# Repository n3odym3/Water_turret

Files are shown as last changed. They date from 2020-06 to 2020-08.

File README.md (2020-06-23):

# Water turret

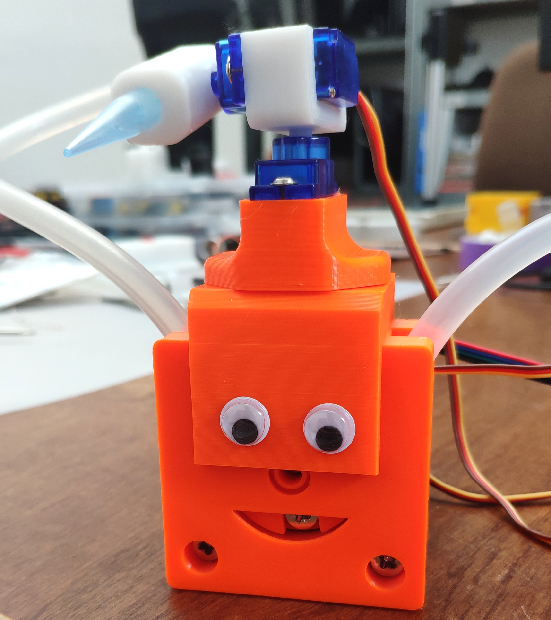
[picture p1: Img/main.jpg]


This water turret uses a WemoD1, two 9g servo motors, a Nema17 stepper motor (+DRV8825 driver) and 3D printed parts to create a water turret that can be remotely controlled via MQTT and automatically aims and shoot water at different locations.

## Supplies
- 6x bearings 13x4x5mm
- 6x M4 washers
- 7x M4 nuts
- 3x M4x15
- 4x M4x25
- 2x M3x13
- 7mm silicone tube
- P1000 micropipette Tip
- 4x 10x3mm neodymium magnets

## Wiring
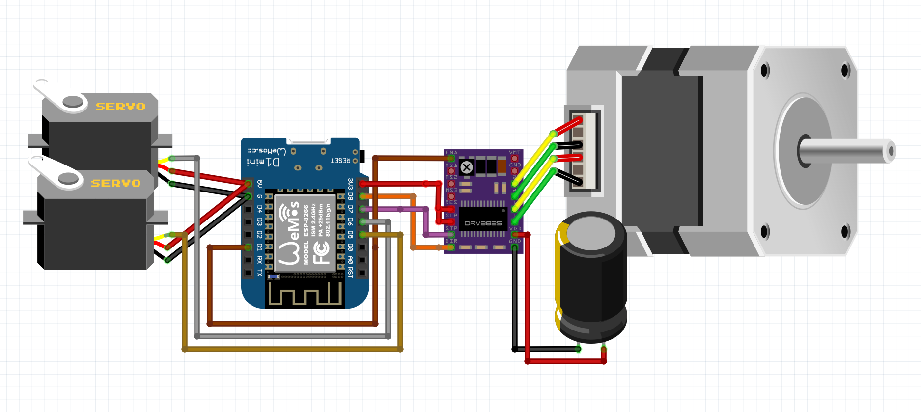
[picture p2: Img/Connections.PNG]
 \
- Servo 1 : D5 (GPIO 14)
- Servo 2 : D6 (GPIO 12)
- DIR : D8 (GPIO 15)
- STEP : D7 (GPIO 14)
- EN : D1 (GPIO 05)
## Control
The robot can be controlled by sending simple JSON commands :
- X axis : {"X": 0 to 180}
- Y axis : {"Y": 0 to 180}
- Pump : {"P" : steps (200 steps/rotation)} \
Ex : {"X": 30, "Y":50} then {"P": 10000}

## NodeRed demo
The demo on NodeRed (installed on a Raspberry Pi zero) allows to test and remote control the robot.\
Sensors and advances automation sequences could be added to the flow to water several plants depending on soil moisture or add a camera with motion detection to make an anti-intrusion system or anything else.

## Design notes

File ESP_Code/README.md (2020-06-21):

# Dependencies
- ArduinoJson6

## Included
- ESP8266WiFi
- PubSubClient
- Servo

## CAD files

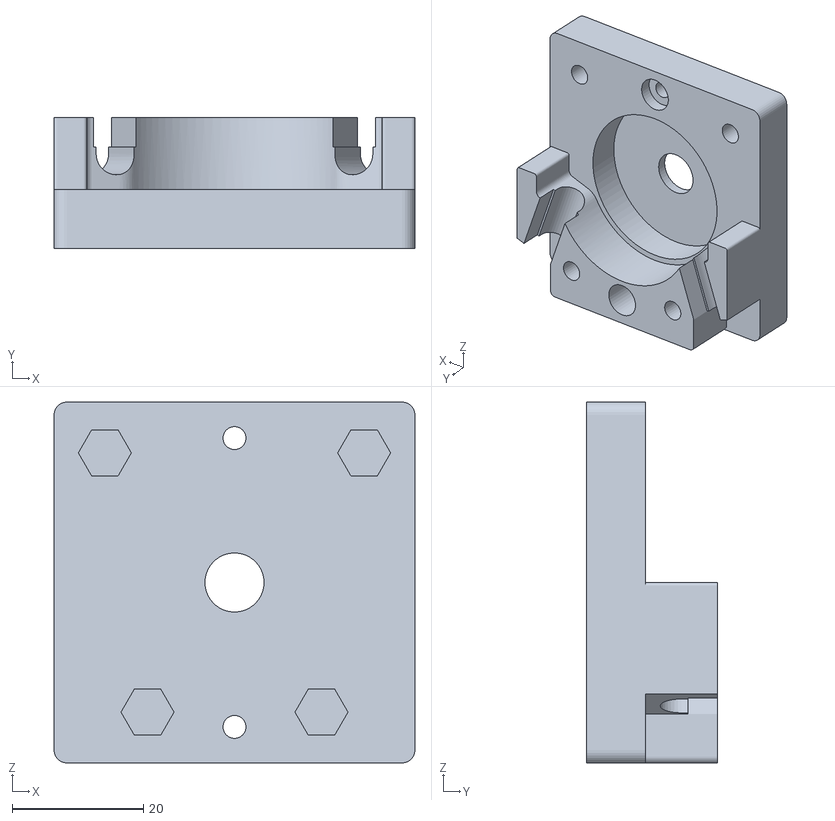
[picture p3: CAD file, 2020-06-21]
3D Files/Stator Main.stl
55.0 x 20.0 x 55.0

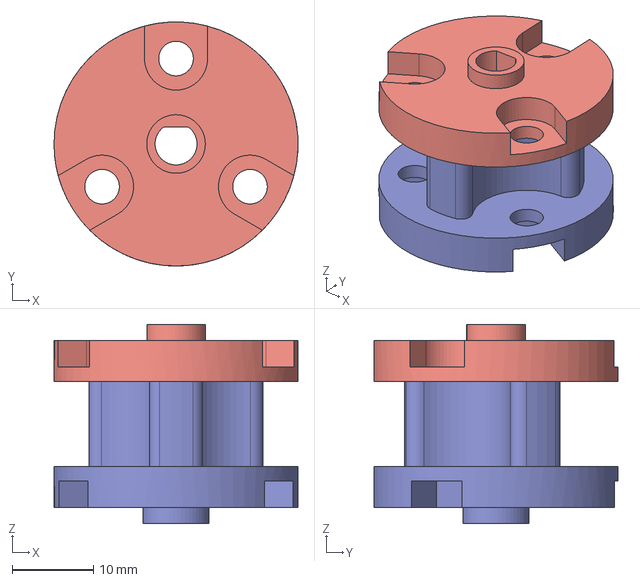
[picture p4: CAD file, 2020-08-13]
3D Files/Rotor.step
30.0 x 30.0 x 24.5 mm

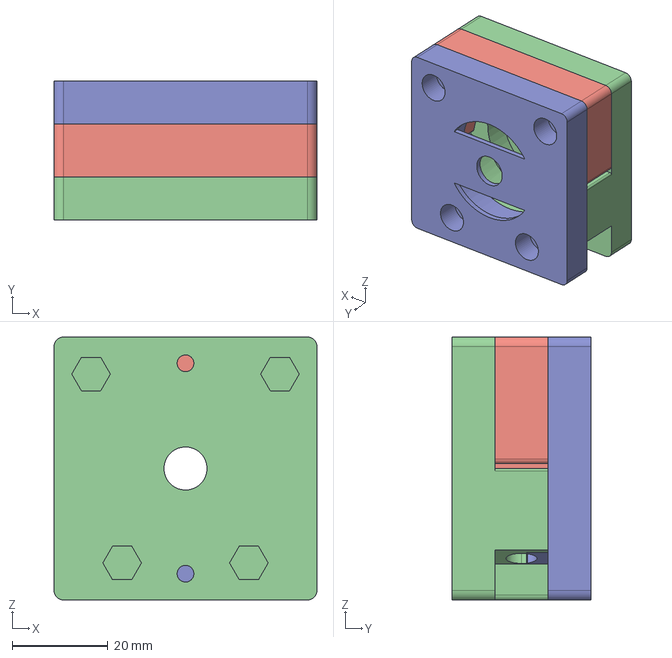
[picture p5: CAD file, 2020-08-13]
3D Files/Stator.step
55.0 x 29.0 x 55.0 mm

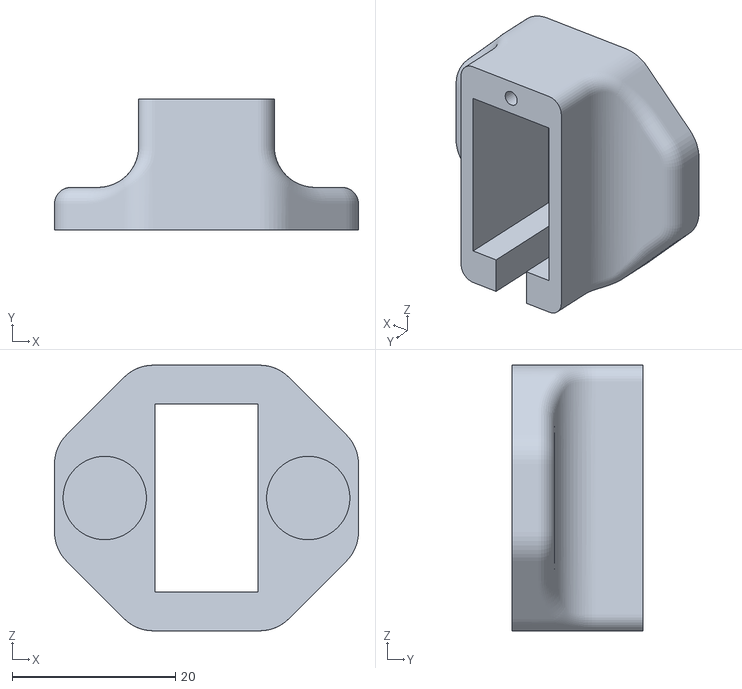
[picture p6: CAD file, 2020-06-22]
3D Files/X_Holder.stl
37.2 x 16.0 x 32.5

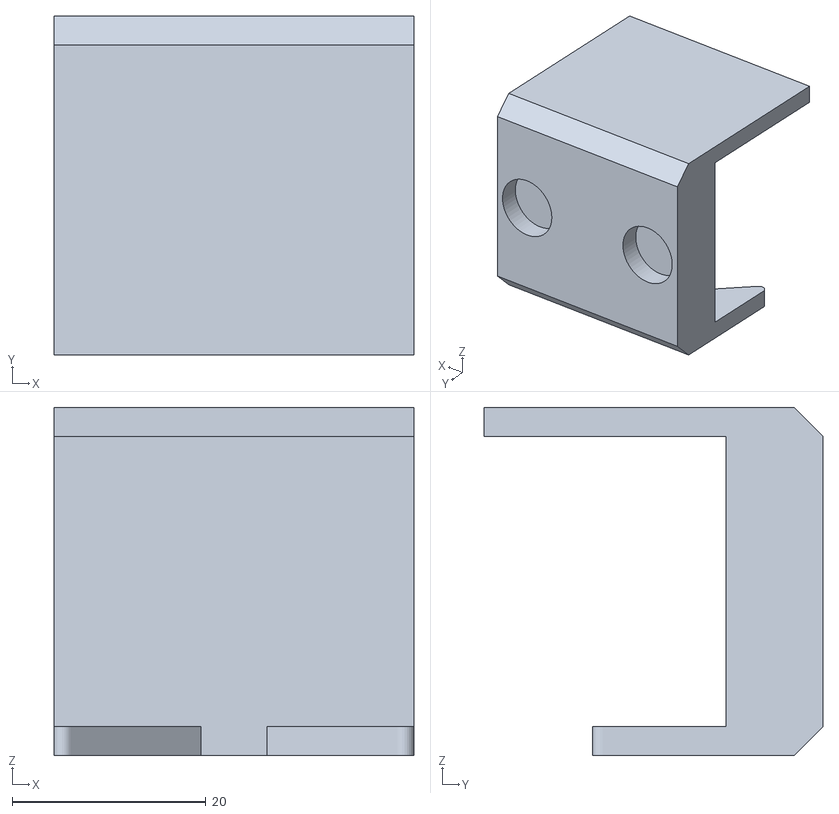
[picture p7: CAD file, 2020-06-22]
3D Files/Motor_Support.stl
37.2 x 35.0 x 36.0

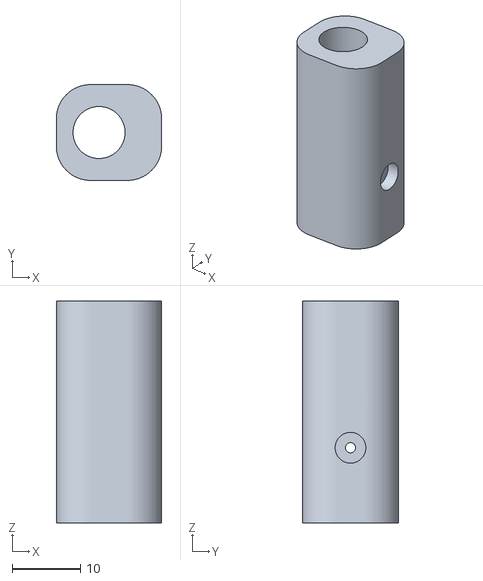
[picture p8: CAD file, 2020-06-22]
3D Files/Tip_Holder.stl
15.4 x 14.0 x 32.4

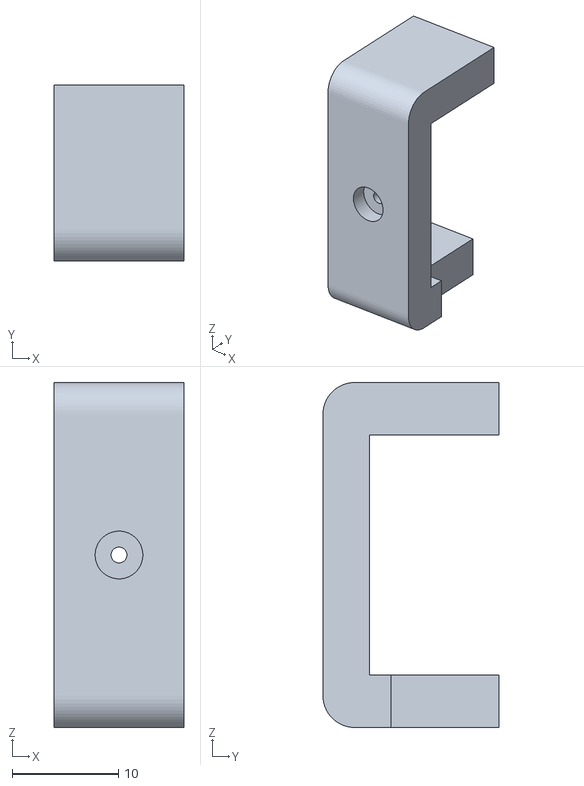
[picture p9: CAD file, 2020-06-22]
3D Files/Y_Holder.stl
12.2 x 16.6 x 32.5

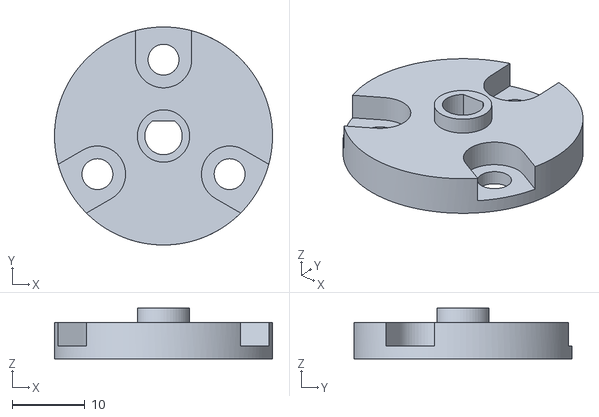
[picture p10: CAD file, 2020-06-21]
3D Files/RotorB.stl
30.0 x 30.0 x 7.00

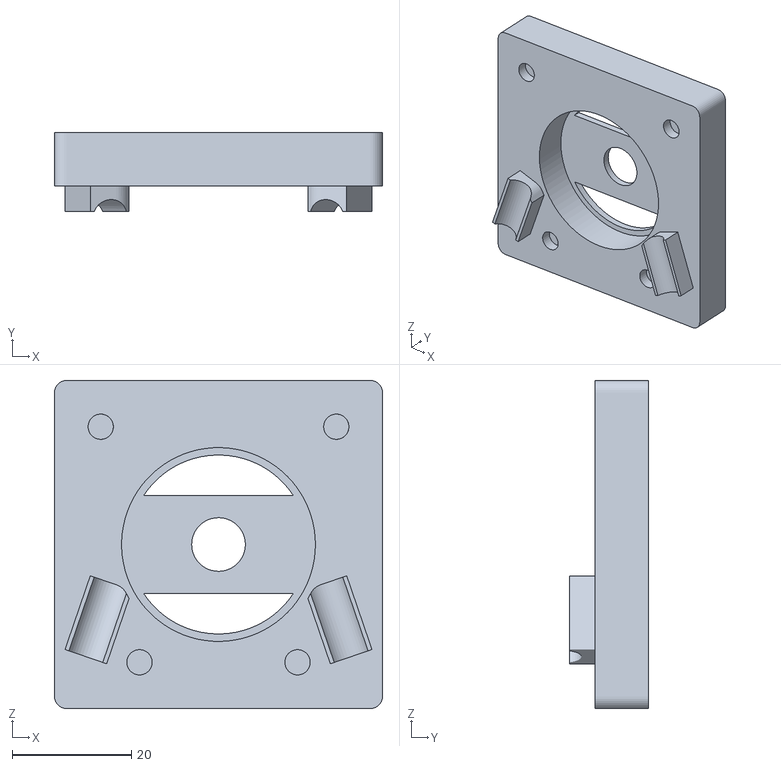
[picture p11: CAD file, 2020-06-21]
3D Files/Stator Lock.stl
55.0 x 13.2 x 55.0

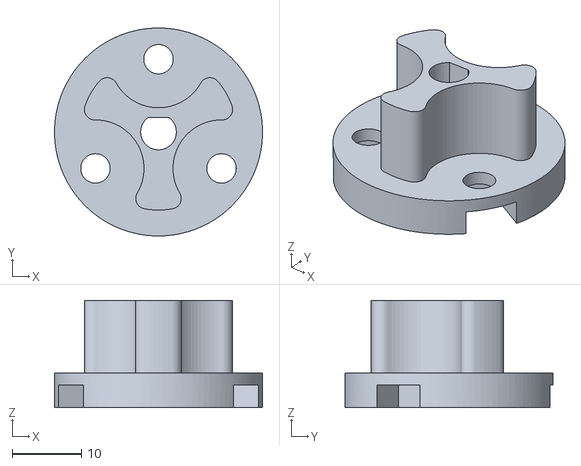
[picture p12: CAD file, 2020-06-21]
3D Files/RotorA.stl
30.0 x 30.0 x 15.5

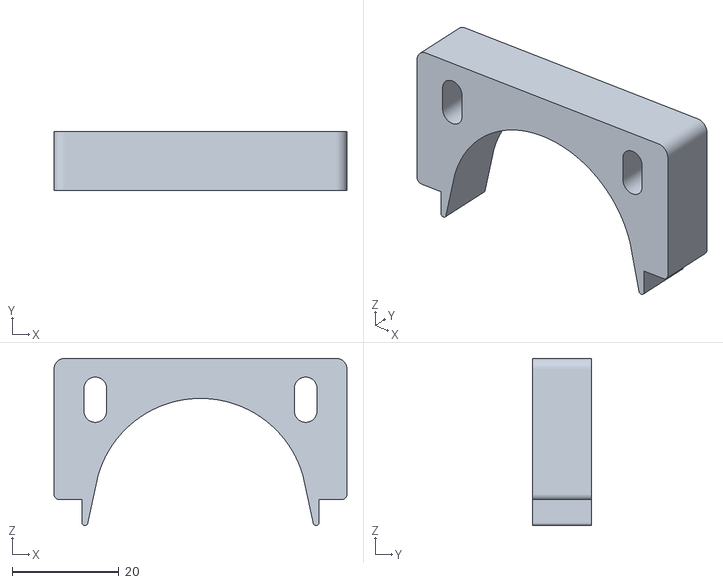
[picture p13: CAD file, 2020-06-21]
3D Files/Lock.stl
55.0 x 11.0 x 31.4

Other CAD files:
3D Files/Rotor.f3d
3D Files/Stator.f3d

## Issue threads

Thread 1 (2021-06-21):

Issue on drv8825 schematic

DaspRoot, 2021-06-21:
In Connections.PNG, there are two mistakes on the schematic:
-The capacitor should be on the step motor supply (VMT and GND)
-Then there is no VDD but rather FLT/

Sorry for the inconvenience

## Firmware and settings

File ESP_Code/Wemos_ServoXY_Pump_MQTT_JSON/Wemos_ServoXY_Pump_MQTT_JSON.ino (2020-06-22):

#include <ESP8266WiFi.h>
#include <PubSubClient.h>
#include <ArduinoJson.h> //ArduinoJSON6
DynamicJsonDocument Input(2048);
#include "config.h"

#include <Servo.h>
Servo ServoX;
Servo ServoY;

#define RPM 200
#define DIR 15// D8
#define STEP 13// D7
#define EN 5// D1

WiFiClient espClient;
PubSubClient client(espClient);

class StepperDriver {
  public:
    short dir_pin, step_pin, en_pin;
    int delay_step = 500;
    StepperDriver(): dir_pin(0), step_pin(0), en_pin(0) {}
    StepperDriver(short dir_pin, short step_pin, short en_pin) : dir_pin(dir_pin), step_pin(step_pin), en_pin(en_pin) {}

    void begin(int rpm) {
      pinMode(dir_pin, OUTPUT);
      pinMode(step_pin, OUTPUT);
      pinMode(en_pin, OUTPUT);

      delay_step = (60000000 / (200 * rpm)) / 2;
    }
    void enable(void) {
      digitalWrite(en_pin, LOW);
    }
    void disable(void) {
      digitalWrite(en_pin, HIGH);
    }
    void move(long steps) {
      if (steps > 0) {
        digitalWrite(dir_pin, LOW);
      }
      else {
        digitalWrite(dir_pin, HIGH);
        steps = -steps;
      }
      for (int i = 0; i < steps; i++) {
        digitalWrite(step_pin, HIGH);
        delayMicroseconds(delay_step);
        digitalWrite(step_pin, LOW);
        delayMicroseconds(delay_step);
        client.loop();
      }
    }
};
StepperDriver Pump(DIR, STEP, EN);

void callback(String topic, byte* message, unsigned int length) {
  String messageTemp;
  for (int i = 0; i < length; i++) {
    messageTemp += (char)message[i];
  }
  Serial.println(messageTemp);
  deserializeJson(Input, messageTemp);
  if (Input.containsKey("X")) {
    ServoX.write(Input["X"]);
  }
  if (Input.containsKey("Y")) {
    ServoY.write(Input["Y"]);
  }
  if (Input.containsKey("P")) {
    Pump.enable();
    Pump.move(Input["P"]);
    Pump.disable();
  }
}

void setup_wifi() {
  delay(10);
  Serial.println();
  Serial.print("Connecting to ");
  Serial.println(ssid);
  WiFi.mode(WIFI_STA);
  WiFi.hostname(HostName);
  WiFi.begin(ssid, password);
  while (WiFi.status() != WL_CONNECTED) {
    delay(500);
    Serial.print(".");
  }
  Serial.println("");
  Serial.println("WiFi connected");
  Serial.println("IP address: ");
  Serial.println(WiFi.localIP());
}

void reconnect() {
  while (!client.connected()) {
    Serial.print("Attempting MQTT connection...");
    if (client.connect(HostName, mqttUser, mqttPassword)) {
      Serial.println("connected");
      client.subscribe(topic_DOWN);
      digitalWrite(LED_BUILTIN, HIGH);
    } else {
      digitalWrite(LED_BUILTIN, LOW);
      Serial.print("failed, rc=");
      Serial.print(client.state());
      Serial.println(" try again in 5 seconds");
      delay(5000);
    }
  }
}

void setup() {
  Serial.begin(115200);
  setup_wifi();
  client.setServer(mqtt_server, 1883);
  client.setCallback(callback);
  pinMode(LED_BUILTIN, OUTPUT);
  digitalWrite(LED_BUILTIN, LOW);
  ServoX.attach(14); //D5
  ServoY.attach(12); //D6
  Pump.begin(RPM);
  Pump.disable();

}

void loop() {
  if (!client.connected()) {
    reconnect();
  }
  client.loop();
}
